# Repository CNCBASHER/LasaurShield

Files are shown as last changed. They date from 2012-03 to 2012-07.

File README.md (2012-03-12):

The LasaurShield is a custom PCB for the [Lasersaur project](http://lasersaur.com). It's an [Arduino](http://arduino.cc/) [shield](http://arduino.cc/en/Main/ArduinoShields) that connects laser, stepper, stepper driver, stepper power, limit switches, door sensor, water chiller sensor, emergency stop sensor, and Arduino. Additionally core safety functions are also hardwired on the board (logic gates). The laser is forced off when any of the following occurs: door opens, chiller off or malfunctions, a limit switch triggers.

The LasaurShield is designed around the SparkFun Eagle Library, their design and CAM job rules. Check out the [SparkFun Tutorial](http://www.sparkfun.com/tutorials/108) if you are new to this. If you are interesting doing your own production run check out [this tutorial](http://www.sparkfun.com/tutorials/109).

The following Eagle library and design files are being used:

- cam/sparkfun-gerb274x.cam
- dru/LasaurShield.dru
- lbr/[SparkFun.lbr]
- lbr/con-phoenix-254.lbr (comes with Eagle)
- lbr/con-phoenix-508.lbr (comes with Eagle)
- lbr/con-weidmueller-sl35.lbr (comes with Eagle)

**DISCLAIMER:** Please be aware that operating a DIY laser cutter can be dangerous and requires full awareness of the risks involved. You build the machine and you will have to make sure it is safe. The instructions of the Lasersaur project and related software come without any warranty or guarantees whatsoever. All information is provided as-is and without claims to mechanical or electrical fitness, safety, or usefulness. You are fully responsible for doing your own evaluations and making sure your system does not burn, blind, or electrocute people.

Some Notes about Using Eagle
=============================

Eagle is quite powerful but also awkward to use. It's easy to forget how to command the UI.

When designing the schematic
------------------------------
- import parts libraries, Library->Use
- some parts like the NAND gates require you to press the "Invoke" button and place power and ground. Don't ask me why.
- Once the schematic is done, run the electrical checks Tools->Erc

When laying out the board
--------------------------
- load design rules, Tools->Drc  (dru/LasaurShield.dru)
- place components, move/rotate to optimize the ratsnest
- color layers as needed, View->Display/hide layers
  - 121 _tsilk  ... is top silkscreen
  - 122 _bsilk  ... is bottom silkscreen
- run autoroute, 
  - The power of the autorouter is that it can be used incrementally. Some wires can be drawn manually and the autorouter can finish the rest. 
  - Another great approach is to draw some wires roughly (e.g. on one side of the board) then autoroute, rip the manual wires and autoroute again. This way the autorouter follows the general idea but draws the wires nicely.
- if the autorouter should use different trace widths this can be accomplished by defining net classes with different widths, Edit->Net classes
  - air wires of the ratsnest (it actually applies to the entire signal) can then be assigned to the various net classes

When creating the CAM Job (gerber files)
-----------------------------------------
- run final design rule check, Tools->Drc
- Open the CAM Processor, File->Cam Processor
- Open the CAM rule file, File->Open->Job   (cam/sparkfun-gerb274x.cam)
- Press "Process Job"
- At this point Eagle creates a bunch of files in the same directory as the board file. 
  - Top Copper (GTL)
  - Top Soldermask (GTS)
  - Top Silkscreen (GTO)
  - Bottom Copper (GBL)
  - Bottom Soldermask (GBS)
  - Bottom Silkscreen (GBO)
  - Drill File (TXT)
  - Drill Summary (dri)
- before sending these to a manufacturing house check them with [Viewplot](http://www.viewplot.com/) or by uploading a zip to [circuitpeople.com](http://circuitpeople.com/).

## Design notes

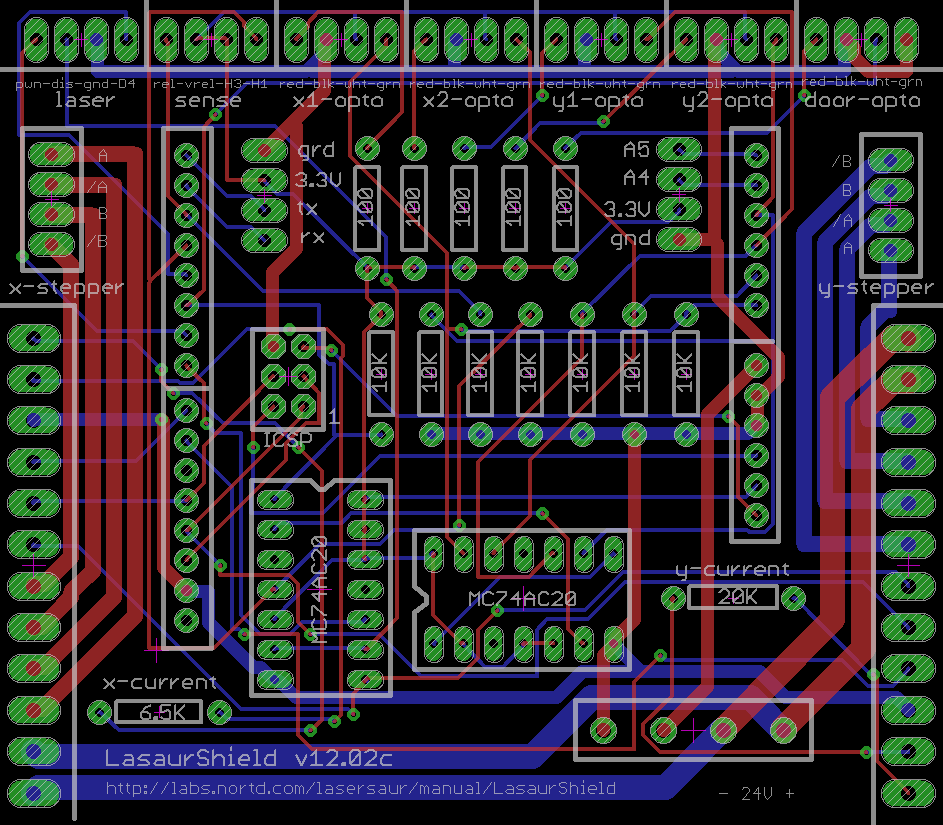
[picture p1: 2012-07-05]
pcb-job-files/LasaurShield.png

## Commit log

2012-03-12 v12.02b changes to the silkscreen
    [LasaurShield.brd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]
2012-03-12 v12.02b changes to the silkscreen, readme updated
2012-07-05 fixed incorrect labels for air assist pins
    [LasaurShield.brd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]
